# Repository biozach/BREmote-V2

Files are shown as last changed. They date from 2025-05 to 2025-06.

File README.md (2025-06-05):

# BREmote V2 - Open Source eFoil and Esk8 remote 
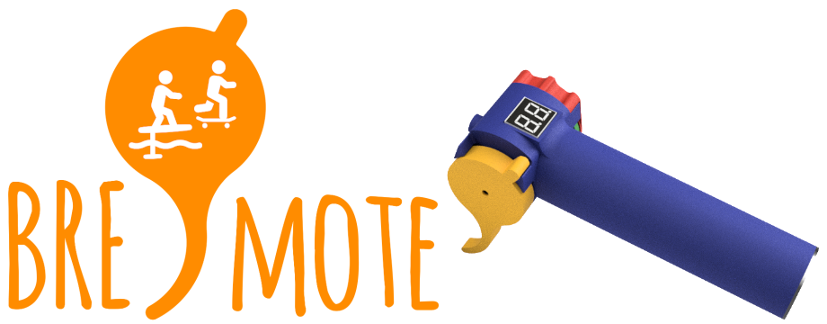
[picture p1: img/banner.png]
Banner


## Features:
* All mechanical parts 3D printed (even the springs)
* Symmetric design
* Sustainable - All external parts can be replaced
* Open Source: 3D Models, Electronics and Software are GPL3.0
* 868/915MHz Link (range dependant on antenna type, position)
* Communication with VESC via UART / CAN
* Low battery alarm (vibration)
* Water ingress alarm integrated in receiver
* Gears / Power Levels / Cruise Control
* Charging and Programming via USB

## Links:
* [Build Video](https://youtu.be/Fw4YdQWvs6I)
* [SW Setup & Config Video](https://youtu.be/r6JIZEq3aTU)
* [Config Tool](https://lbre.de/BREmote/struct.html)
* [Serial Terminal](https://lbre.de/BREmote/sertest.html)
* [Expo Tool](https://lbre.de/BREmote/expo.html)
* [Flash Download Tool](https://dl.espressif.com/public/flash_download_tool.zip)

## Usage:

## Status/Error Codes:
Tx:
* Ex : Remote Errors
* EP: Not paired
* EC: Not Cald
* ESV: Error Config version SPIFFS <> Build
* ESP3: Error init SPIFFS
* ESP4: Error writing SPIFFS
* EHFC: Error HF (LoRa) setting
* EHFI: Error HF (LoRa) init
* EHFP: Error transmit power
* ECH: Error charger

Rx:
* Aux blink:
	* 3x: Error init SPIFFS
	* 2x: Error Config version SPIFFS <> Build
	* 4x: Error writing SPIFFS

* Bind blink:
	* Short Periodic Flash: Not paired
	* Blink: Paired not connected
	* Solid: Connected
	
	* 2: Error transmit power
	* 3: Error HF (LoRa) setting
	* 4: Error HF (LoRa) init

## Inputs at startup:
Tx:
* Left: Calibrate
* Right: Pair
* THR+Left: USB Mode
* THR+Right: Delete Spiffs

Rx:
* Bind pushed: Pair
* Both pushed: Delete config

# Connection Examples:

<details>
<summary>VESC with UART</summary>

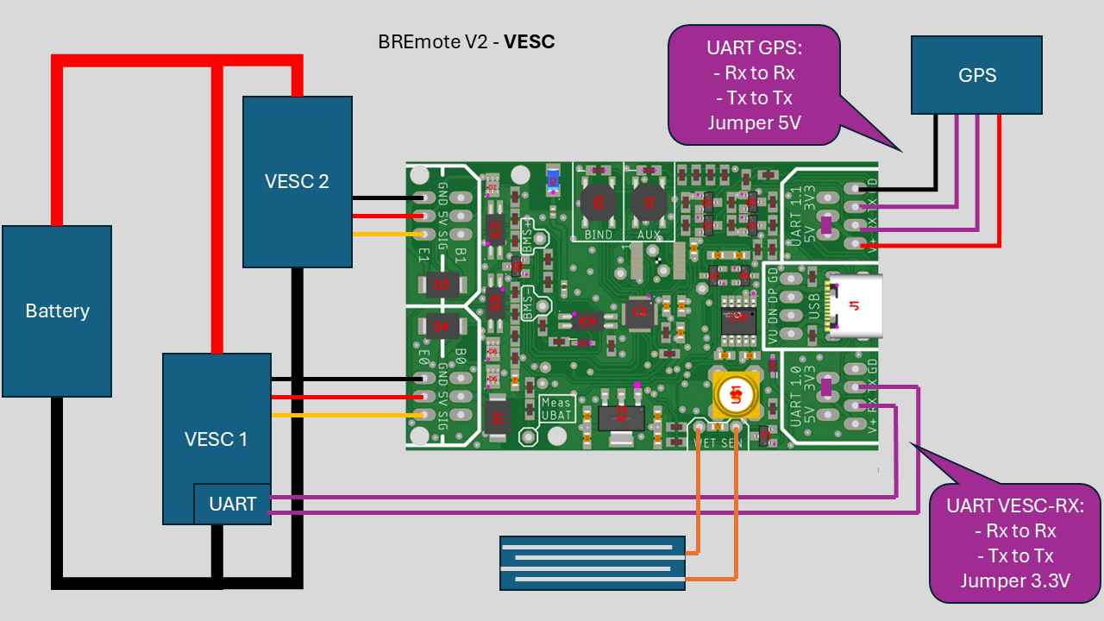
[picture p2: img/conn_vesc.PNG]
Conn


</details>

<details>
<summary>ESC with BREmote BEC</summary>

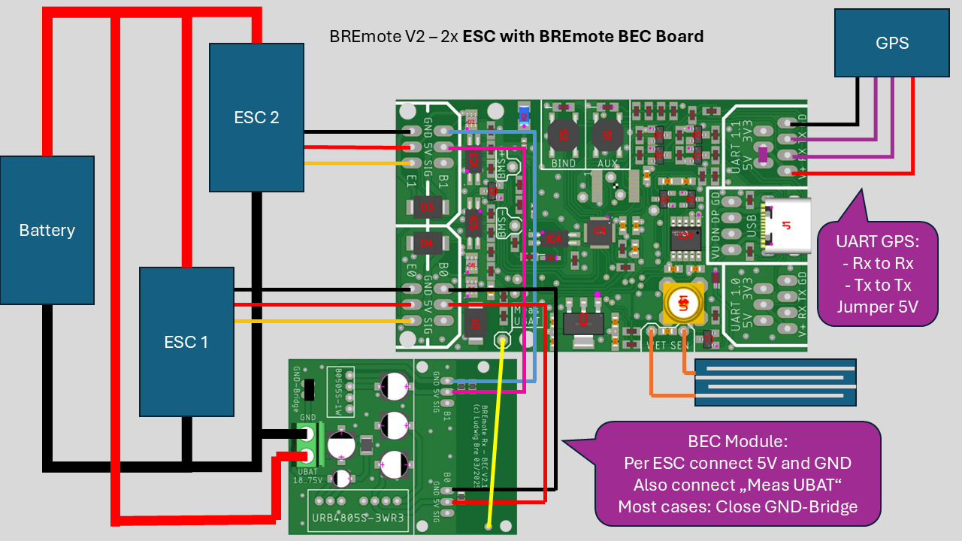
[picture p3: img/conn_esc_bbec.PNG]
Conn


</details>

<details>
<summary>ESC with own BEC</summary>

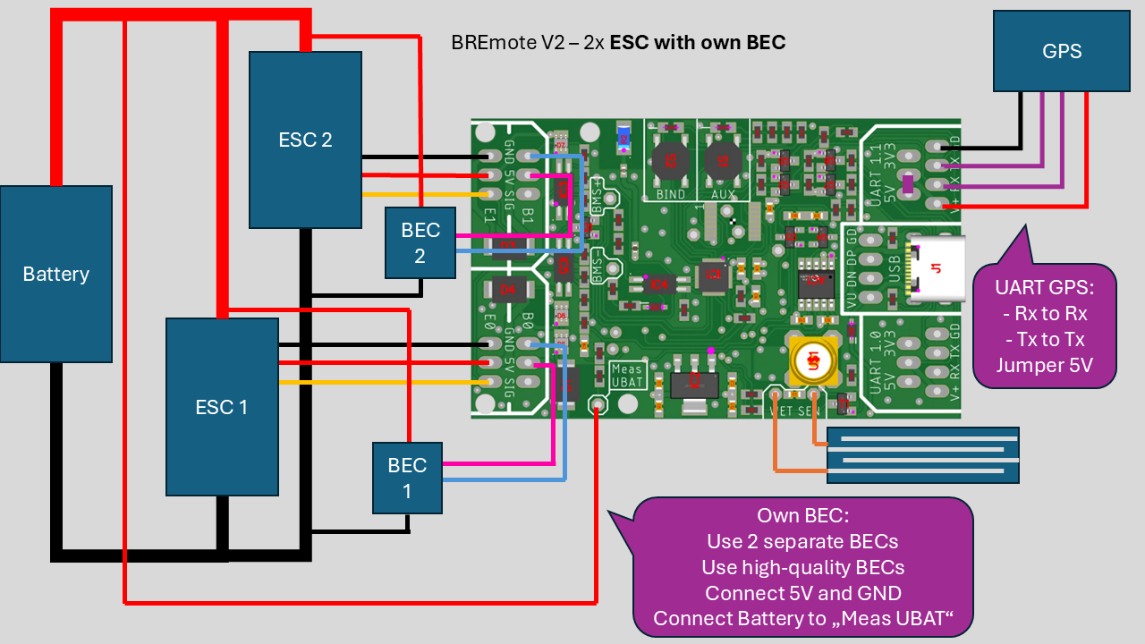
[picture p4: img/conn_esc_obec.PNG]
Conn


</details>

<details>
<summary>VESC + Servo</summary>

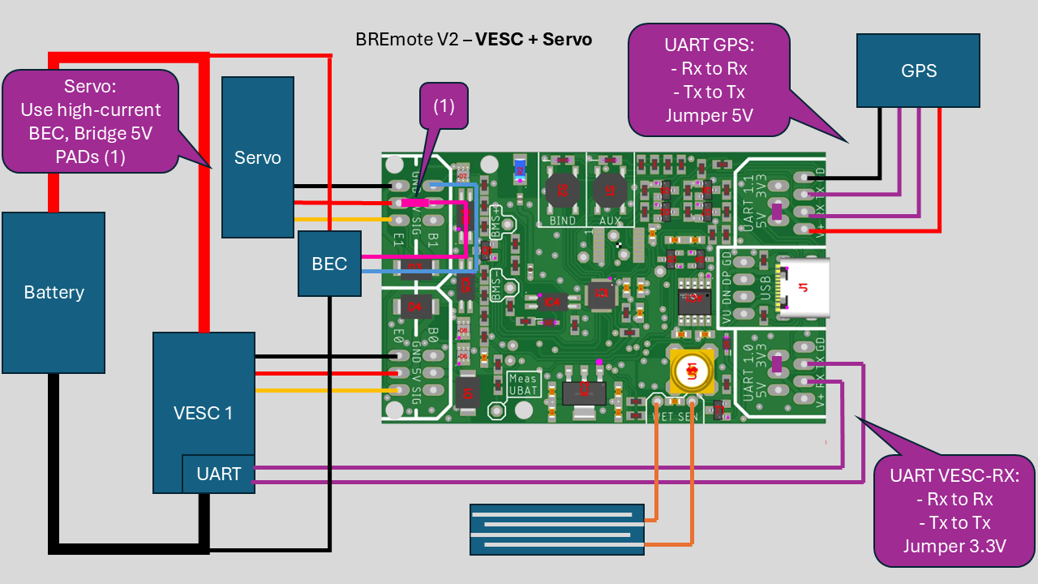
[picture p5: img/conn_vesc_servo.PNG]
Conn


</details>

<details>
<summary>ESC + Servo</summary>

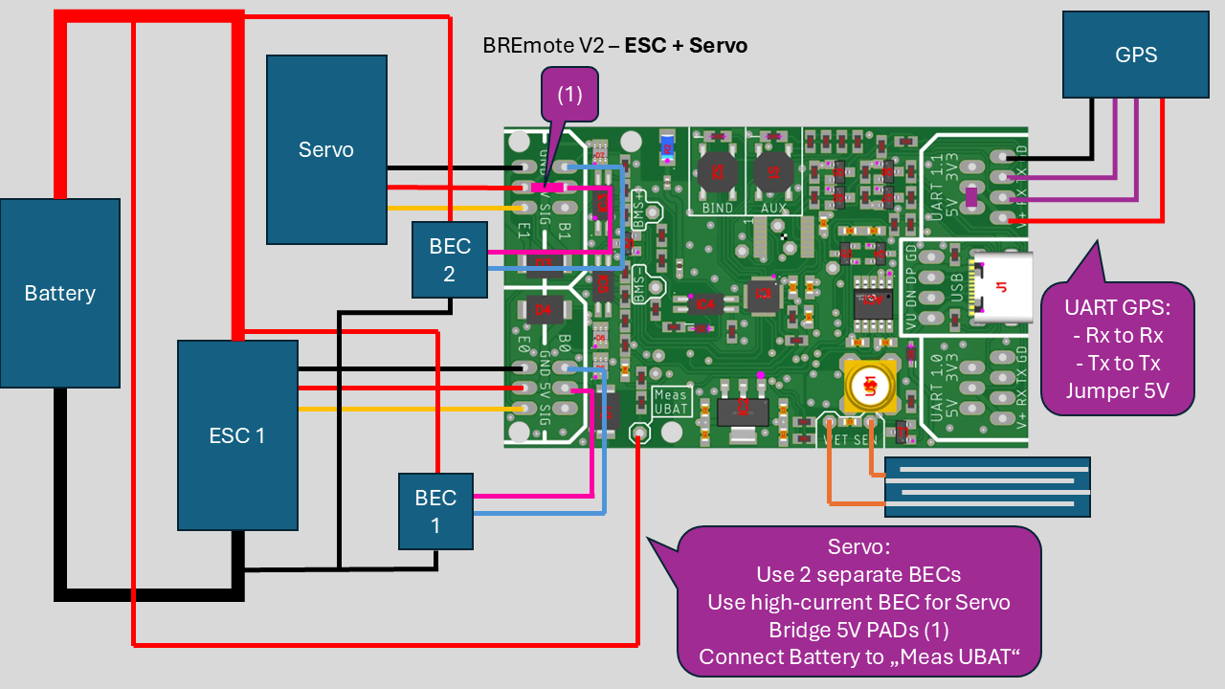
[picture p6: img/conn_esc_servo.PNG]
Conn


</details>

# Changelog:
### 2025-06-05:
Updated Readme (Add YT link and conn examples)
### 2025-05-26:
Updated Complete.step (spring assy. missing)
Added RF settings for US/AU(915MHz) in Tx&Rx
### 2025-05-20: [Release V2.1]
Initial release

---
# Credits:
Logo uses "watersport" and "Skate" by Adrien Coquet from https://thenounproject.com/. CC BY 3.0.

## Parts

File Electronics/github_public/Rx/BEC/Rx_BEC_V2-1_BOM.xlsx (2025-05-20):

Comment | Designator | Footprint | JLCPCB Part #（optional）
100uF 35V RVE100UF35V67RV0072 | C3 | CPOL-EU153CLV-0605 | C2836437
10uF 100V RVT2A100M0607 | C2, C4, C5 | CPOL-EU153CLV-0605 | C86606 | C72482
10uH 900mA CBC3225T100KR | L1 | R-EU_R1210 | C90321
1uF 100V HT2A1R0M0405 | C1 | CPOL-EU153CLV-0405 | C87863
470 | R1, R2, R3 | R-EU_R0805
WJ126V-5.0-2P | U$1 | WJ126V-5.0-2P | C8404

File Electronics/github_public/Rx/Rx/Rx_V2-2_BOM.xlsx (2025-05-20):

Comment | Designator | Footprint | JLCPCB Part #（optional）
0R | R_ANT | R-EU_R0402
100 | R7, R8 | R-EU_R0603
100n | C1, C2, C3, C4, C7, C8, C9, C10, C13, C16 | C-EUC0603
10k | R4, R10, R11, R15, R20, R24, R28, R30, R31, R32, R33, R34, R35, R36, R37 | R-EU_R0603
120k | R1 | R-EU_R0603
1M | R22 | R-EU_R0603
1N4148WS | D2, D5 | 1N4148WS | C2128
1k | R9, R14, R38, R39, R40, R41, R42 | R-EU_R0603
1u | C5, C6, C12 | C-EUC0603
2.2uF | C11 | C-EUC0603
220 | R25, R26 | R-EU_R0603
3k3 | R12 | R-EU_R0603
4k7 | R13, R16, R17, R18 | R-EU_R0603
5k1 | R5, R6 | R-EU_R0603
LQW15AN6N8G00D | L_ANT1 | R-EU_R0402 | C82919
74HC4052PW,118 | IC6 | 74HC4052PW,118 | C19723807
AMS1117-3.3 | IC2 | AMS1117-3.3 | C6186
AO3400A | Q3, Q4 | AO3400A | C20917
AW9523BTQR | IC1 | AW9523BTQR | C148077
BSS138 | Q1, Q2, Q5, Q6, Q7 | BSS138 | C5224260
CH340K | AC1 | CH340K | C968586 | alt C18208922
EL3H7_TA_-VG | IC3, IC4, IC5 | EL3H7_TA_-VG | C32565
LM66100DCKR | D6, D7, D8 | LM66100DCKR | C2869734
MMBT5551 | T1 | BC847B-NPN-SOT23-BEC | C2145
KT-0603R | LED2, LED3 | LEDCHIP-LED0805 | C2286
P6SMB6.8CA | D1, D3, D4 | P6SMB6.8CA | C78395
RFANT3216120A5T | R2 | R-EU_R1206 | C127629
BWSMA-KE-Z001 | U$1 | SMA_5.08_1.4 | C496549
TS-1187A-B-A-B | S1, S2 | TS-1187A-B-A-B | C318884
TYPE-C-31-M-12 | J1 | TYPE-C-31-M-12 | C165948

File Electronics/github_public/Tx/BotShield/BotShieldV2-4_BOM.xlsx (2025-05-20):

Comment | Designator | Footprint | JLCPCB Part #（optional）
100 | R4 | R-EU_R0603
100n | C5, C6, C9, C10, C13, C14, C15, C17, C20 | C-EUC0603
10k | R10, R11, R13, R14, R15, R16, R17, R22 | R-EU_R0603
10n | C12 | C-EUC0603
10u | C7, C8, C16 | C-EUC0603
1k | R3, R7, R12, R20, R21 | R-EU_R0603
1u | C18, C19 | C-EUC0603
2.2uF | C11 | C-EUC0603
3k3 | R6, R18 | R-EU_R0603
4k7 | R5, R8, R9 | R-EU_R0603
6k8 | R19 | R-EU_R0603
74LVC1G14GW,125 | IC3 | 74LVC1G14GW,125 | C265125
ADS1115IDGSR | IC5 | ADS1115IDGSR | C37593
AO3400A | Q2, Q3, Q4, Q5 | AO3400A | C20917
AO3401A | Q6 | AO3401A | C15127
CH340K | AC1 | CH340K | C18208922 | alt C968586
DW01A | IC4 | DW01A-G | C2927799 | alt C18164398 or C351410
FPC-05F-14PH15 | U$11 | FPC-05F-14PH15 | C2856818
FS8205A | Q1 | FS8205A | C2830320
ME6211C33M5G-N | IC6 | ME6211C50M5G | C82942
OH49E-S | IC8 | DRV5055A3QDBZR | C85573
SDFL2012Q2R7KTF | L2 | SDFL2012Q2R7KTF | C1046
TP4056 | IC7 | TP4056-42-ESOP8 | C725790

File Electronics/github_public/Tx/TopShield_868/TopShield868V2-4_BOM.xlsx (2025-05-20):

Comment | Designator | Footprint | JLCPCB Part #（optional）
0R | R1 | R-EU_R0603
100n | C1, C3, C4 | C-EUC0603
10k | R23 | R-EU_R0603
np | R24 | R-EU_R0603
LQW15AN4N3B00D | L_ANT | R-EU_R0402 | C91625
GJM1555C1H4R0BB01D | C_ANT | C-EUC0402 | C161323
1u | C2 | C-EUC0603
LQW15AN6N8G00D | L_ANT1 | R-EU_R0402 | C82919
FPC-05F-14PH15 | U$6 | FPC-05F-14PH15 | C2856818
HT16K33A-24SSOP | U$1 | HT16K33A | C5444736 | alt C5444738
OH49E-S | IC1 | DRV5055A3QDBZR | C85573
RFANT3216120A5T | R2 | R-EU_R1206 | C127629
SDFL2012Q2R7KTF | L1 | SDFL2012Q2R7KTF | C1046
UHE4913G-AE3-R | IC2 | DRV5055A3QDBZR | C86815

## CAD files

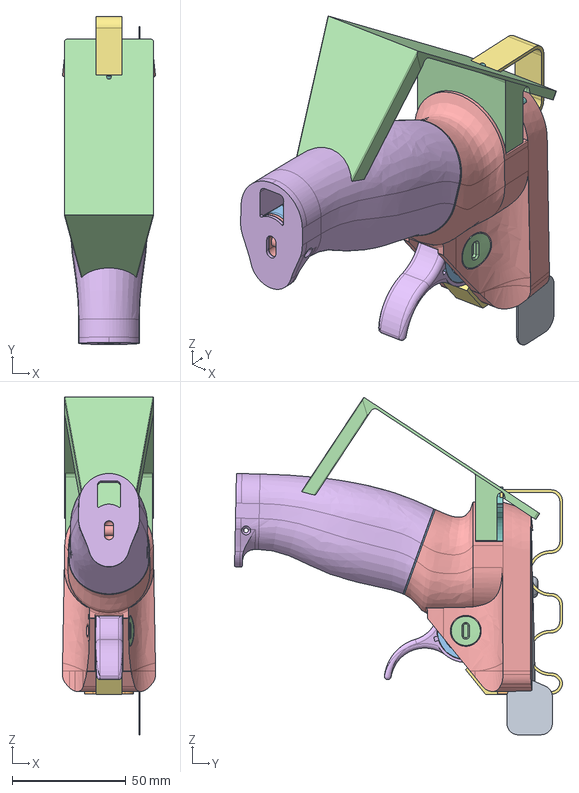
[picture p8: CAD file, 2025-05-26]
Mechanics/Complete.step
41.0 x 144.3 x 148.6 mm
Switch_Side
V2_Spring_Metal v1

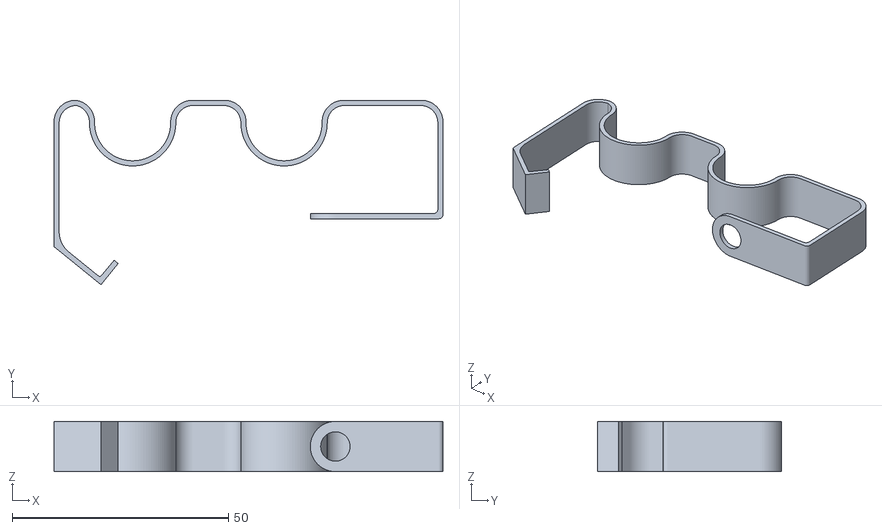
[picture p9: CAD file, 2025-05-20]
Mechanics/Assy_Clamp.stl
90.0 x 42.7 x 11.6

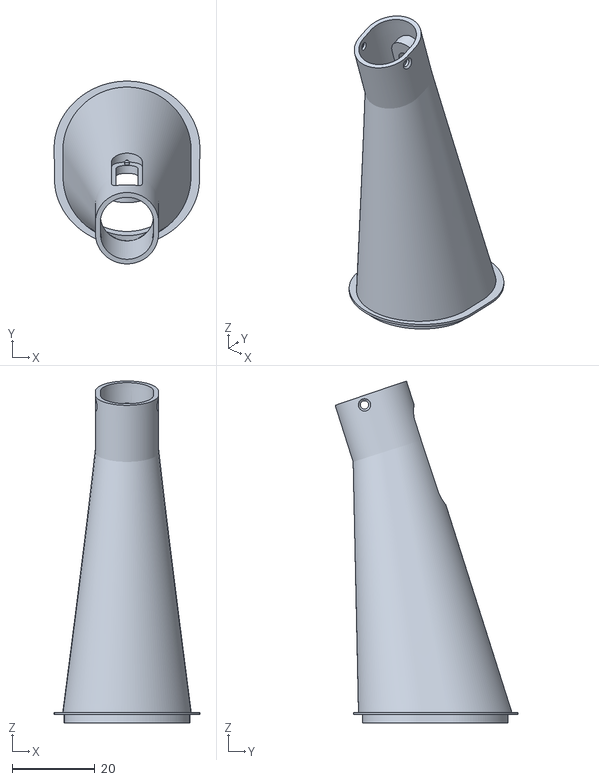
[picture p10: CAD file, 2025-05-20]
Mechanics/InsideHandle.stl
35.3 x 44.3 x 82.9

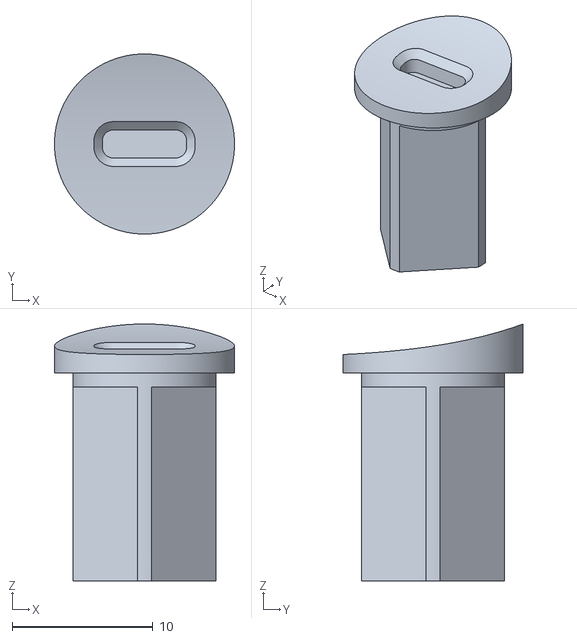
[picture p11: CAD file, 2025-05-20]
Mechanics/Trigger_Pin.stl
12.8 x 12.8 x 18.3

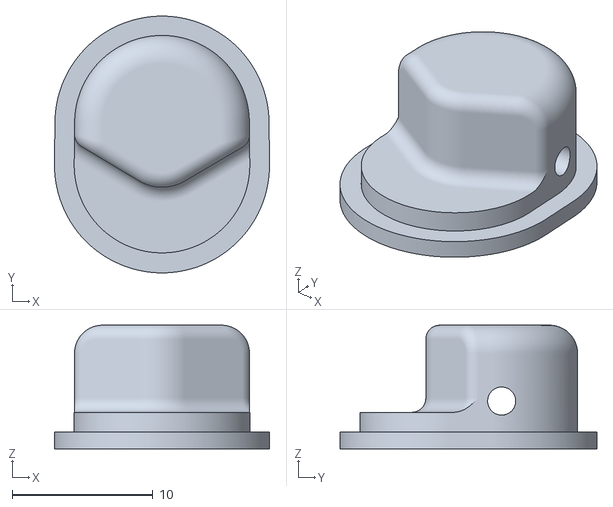
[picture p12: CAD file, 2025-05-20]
Mechanics/Endcap_Handle.stl
15.3 x 18.3 x 8.80

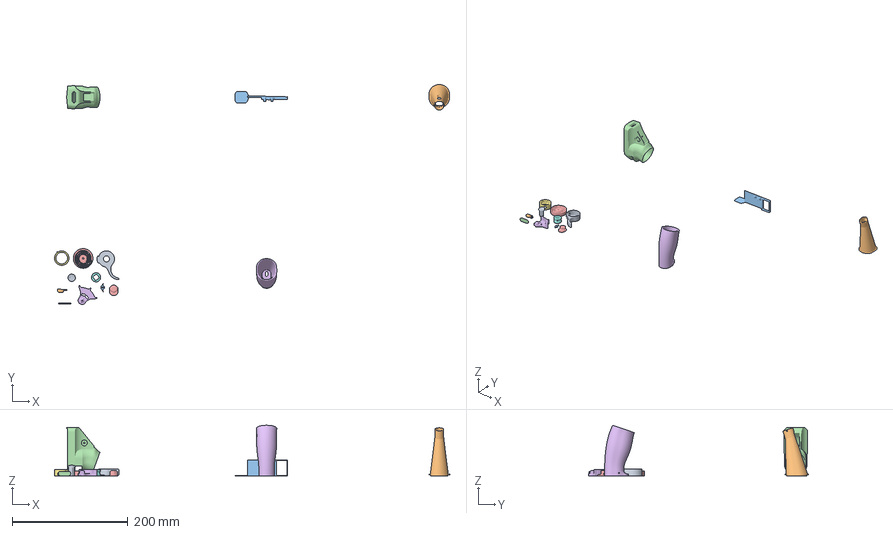
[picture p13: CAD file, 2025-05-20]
Mechanics/AllPartsSliced_V2-1.3mf
681.3 x 379.3 x 87.2 mm
XX_Trigger_export_steep.stl
XX_InsideHandle.stl
XX_Top_Cover.stl
Top.stl
Stator_export.stl
Rotor.stl
XX_Spring_Idle_Mod_Rot (1) (1).stl
XX_Spring_Idle_Mod_Rot (1).stl
XX_Trigger_Pin_Export.stl
Switch.stl
Switch_Cover.stl
FrontPlate.stl
Endcap_Handle.stl
HandleSmall.stl

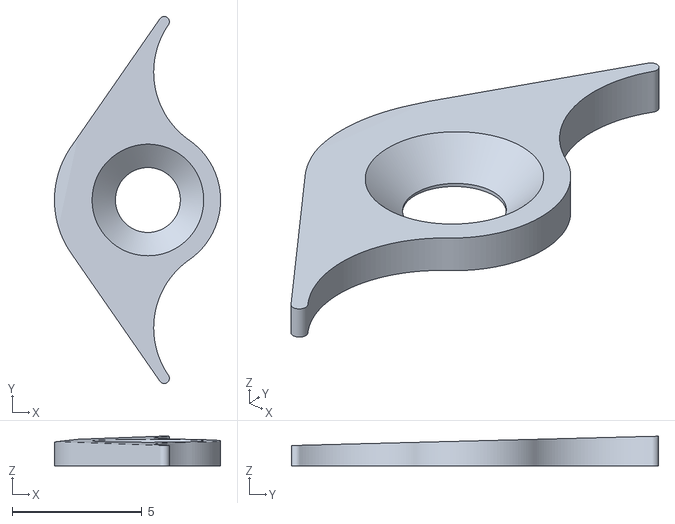
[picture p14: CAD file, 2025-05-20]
Mechanics/Switch_Cover.stl
6.40 x 14.1 x 1.14

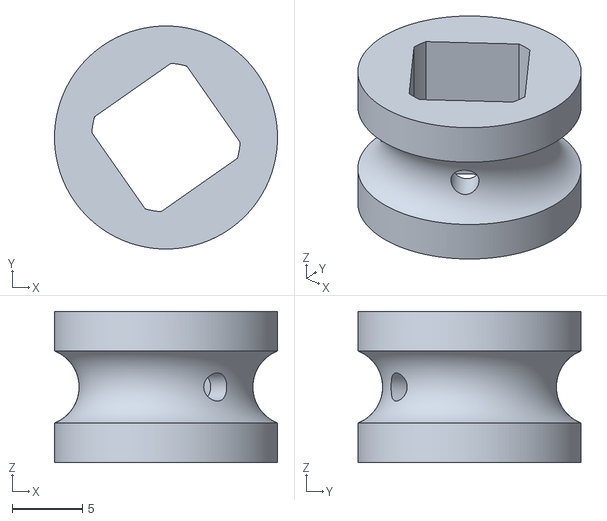
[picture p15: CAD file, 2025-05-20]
Mechanics/Trigger_Spring_2.stl
15.9 x 15.9 x 10.8

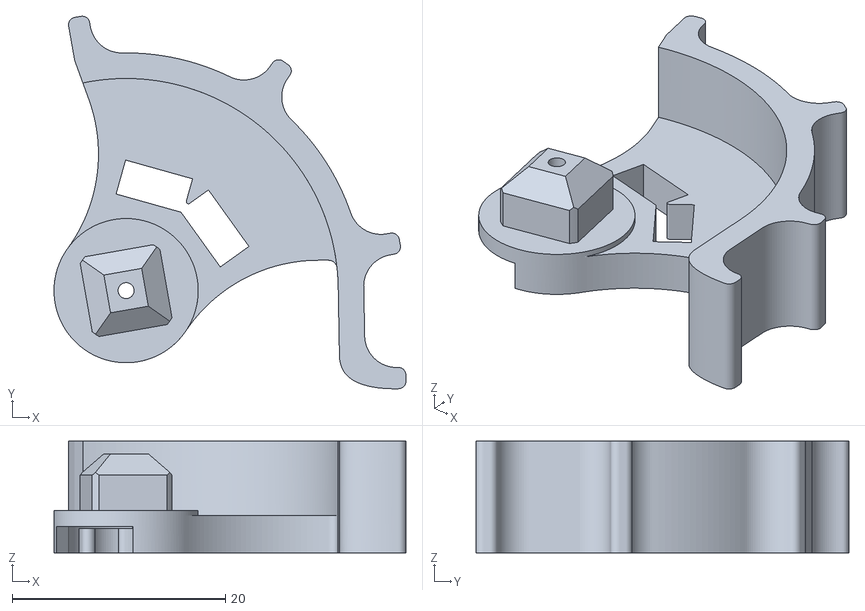
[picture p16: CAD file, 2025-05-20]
Mechanics/Rotor_sidegrip.stl
33.0 x 35.0 x 10.5

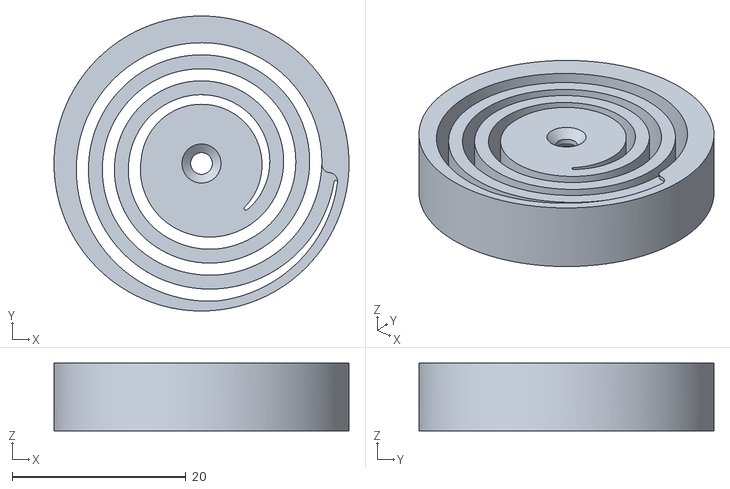
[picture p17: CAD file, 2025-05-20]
Mechanics/Stator.stl
34.0 x 34.0 x 7.80

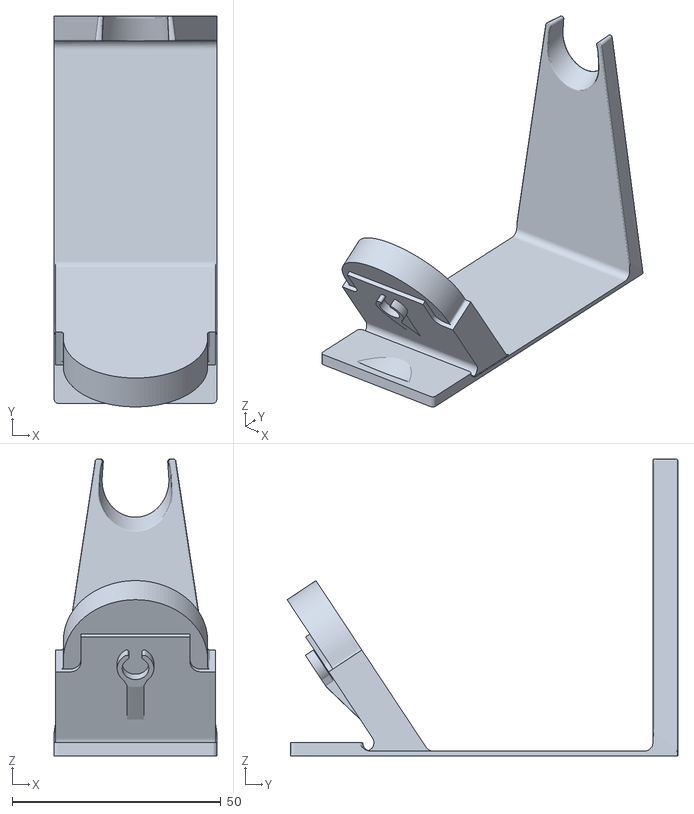
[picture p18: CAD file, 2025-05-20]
Mechanics/FillStand.stl
39.0 x 93.7 x 71.2

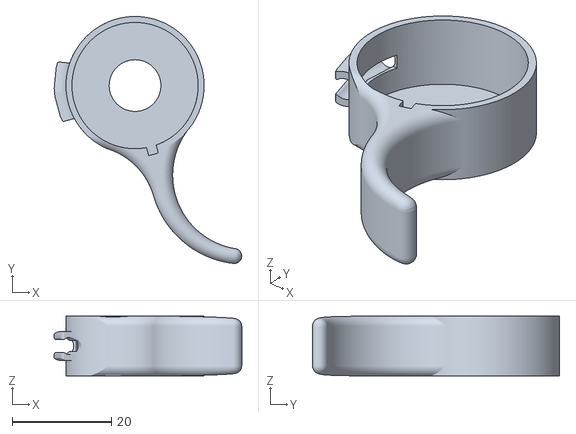
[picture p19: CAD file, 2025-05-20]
Mechanics/Trigger.stl
37.7 x 49.7 x 12.0

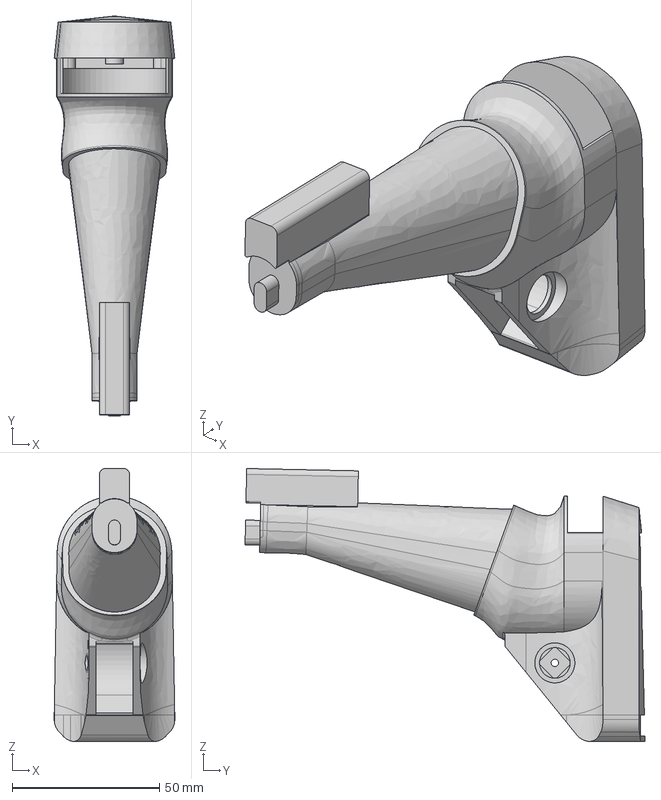
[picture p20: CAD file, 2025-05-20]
Mechanics/HandleCutter.step
41.0 x 135.9 x 92.8 mm

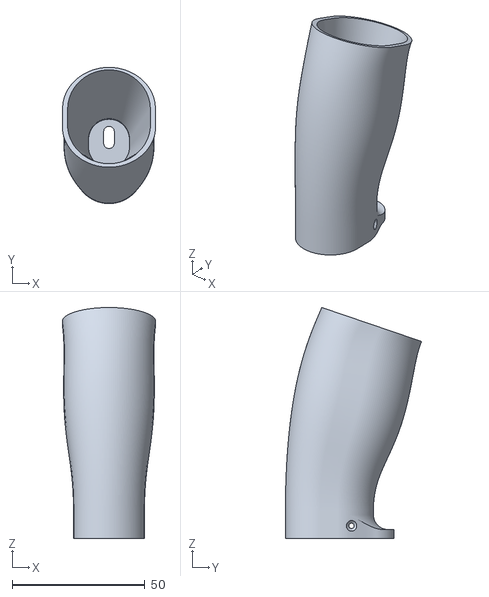
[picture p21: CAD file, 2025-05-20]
Mechanics/HandleSmall.stl
35.2 x 51.4 x 87.2

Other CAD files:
Mechanics/Trigger_Spring_1.stl
Mechanics/Top.stl
Mechanics/Switch.stl
Mechanics/Rotor.stl
Mechanics/FrontPlate.stl
Mechanics/Top_Cover.stl

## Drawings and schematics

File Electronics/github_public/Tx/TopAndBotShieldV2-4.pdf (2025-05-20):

05.05.2025 14:25 f=0.80 C:\Users\rcb8fe\Desktop\prep_order\Tx\final\github_public\TopAndBotShieldV2-4.sch (Sheet: 1/1) ¹⁰uF shared with TP⁴⁰⁵⁶ | 24⁻pin: Place 0R
R7 6 | C¹

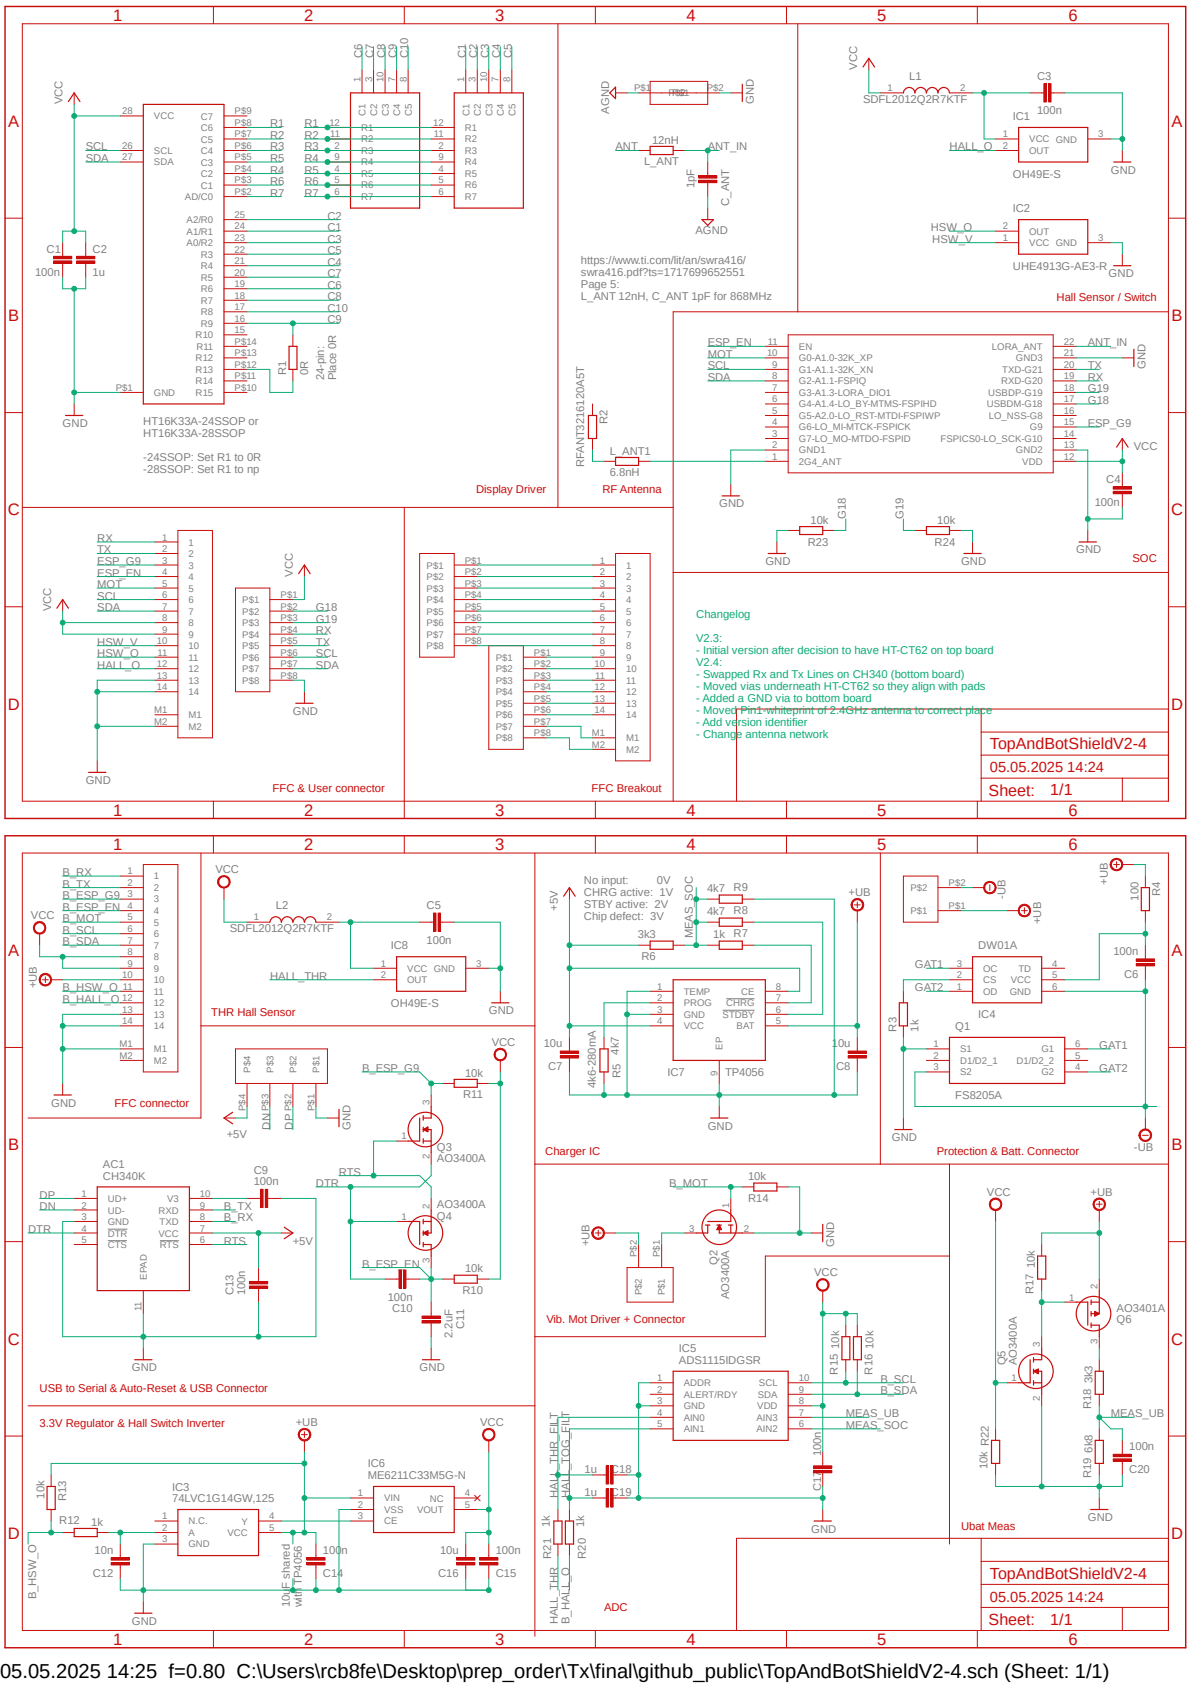
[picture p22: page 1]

SDFL2012Q2R7KTF VCC GND AGND VCC

https://www.ti.com/lit/an/swra416/
swra416.pdf?ts=1717699652551
Page 5:
L_ANT 12nH, C_ANT 1pF for 868MHz

Changelog
- Initial version after decision to have HT-CT62 on top board
- Swapped Rx and Tx Lines on CH340 (bottom board)
- Moved vias underneath HT-CT62 so they align with pads
- Added a GND via to bottom board
- Moved Pin1-whiteprint of 2.4GHz antenna to correct place
- Add version identifier
- Change antenna network

VCC | No input: 0V

Vib. Mot Driver + Connector

USB to Serial & Auto-Reset & USB Connector

VCC 10k
3.3V Regulator & Hall Switch Inverter

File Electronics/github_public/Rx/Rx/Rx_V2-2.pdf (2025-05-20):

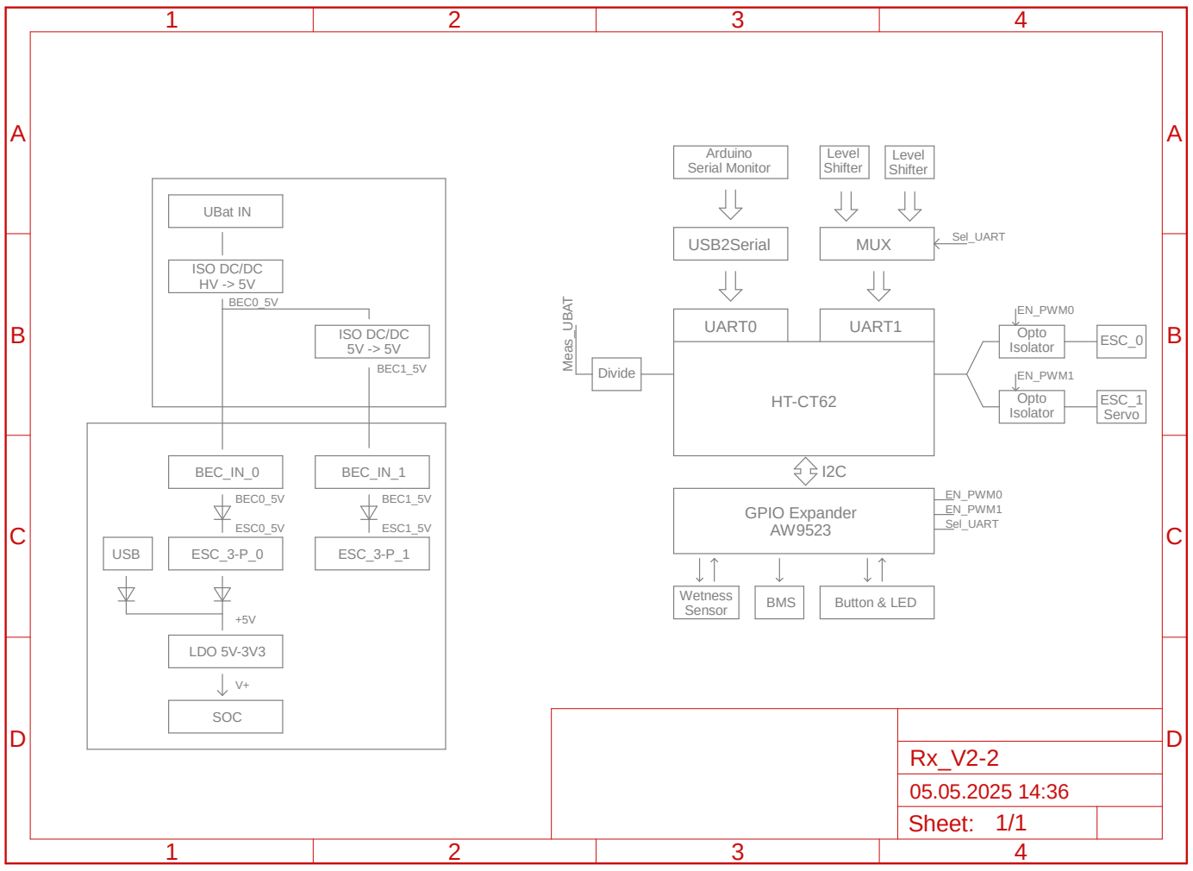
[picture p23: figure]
UART0; UART1; USB2Serial; MUX; Level Shifter; Arduino Serial Monitor; Opto Isolator; ESC_0; ESC_1 Servo; EN_PWM0; EN_PWM1; Sel_UART; Divide Meas_UBAT; GPIO Expander AW9523; I2C Wetness Sensor; BMS; Button & LED; EN_PWM0 EN_PWM1 Sel_UART; BEC_IN_0; ESC_3-P_0; LDO 5V-3V3; BEC_IN_1; ESC_3-P_1; SOC; ISO DC/DC HV -> 5V; ISO DC/DC; 5V -> 5V UBat IN; USB; ESC0_5V; BEC0_5V; BEC1_5V; ESC1_5V; Sheet:

05.05.2025 14:57 f=1.05 C:\Users\rcb8fe\Desktop\prep_order\Tx\final\openfoil\Rx\Rx_V2-2.sch (Sheet: 1/1)

# 1k GND

# IC3 A

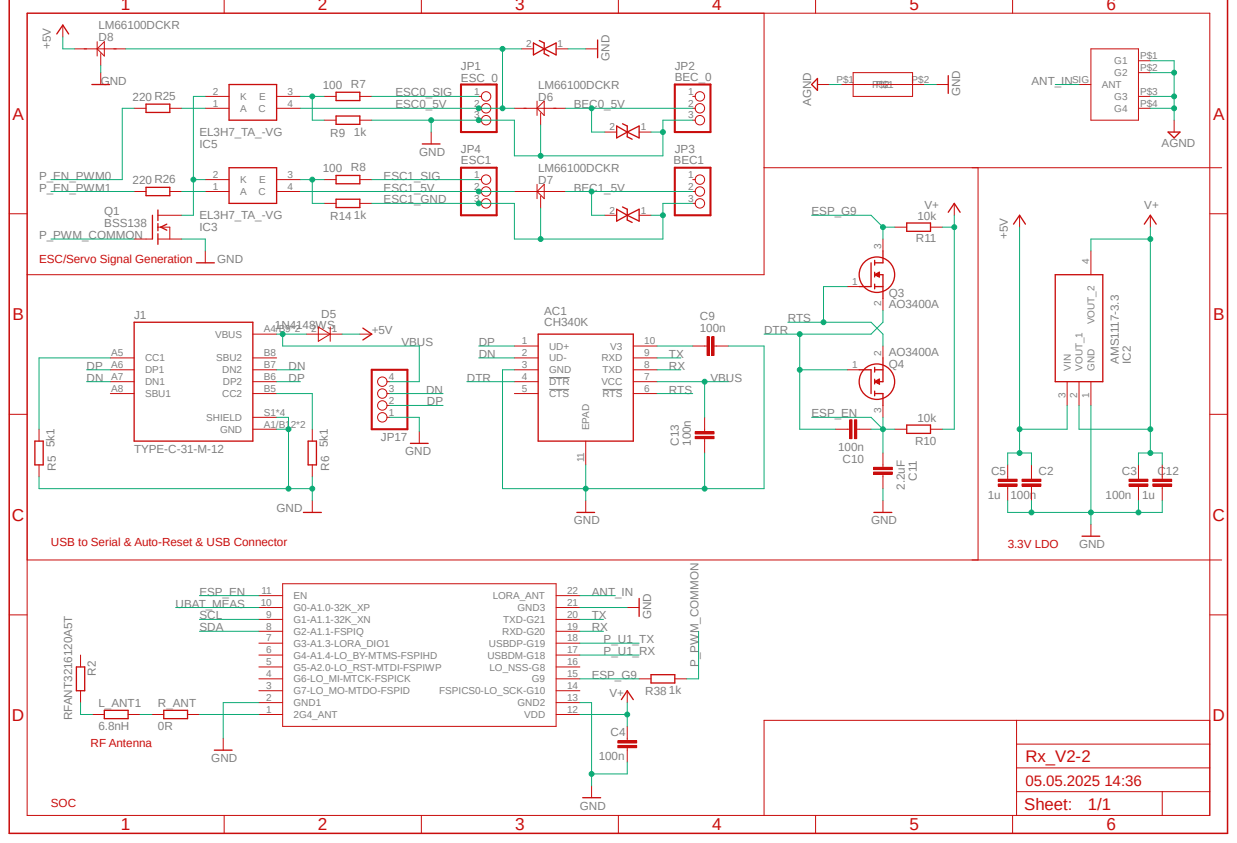
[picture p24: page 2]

ESC/Servo Signal Generation

V+ | BSS¹³⁸ 10k | 10k

A

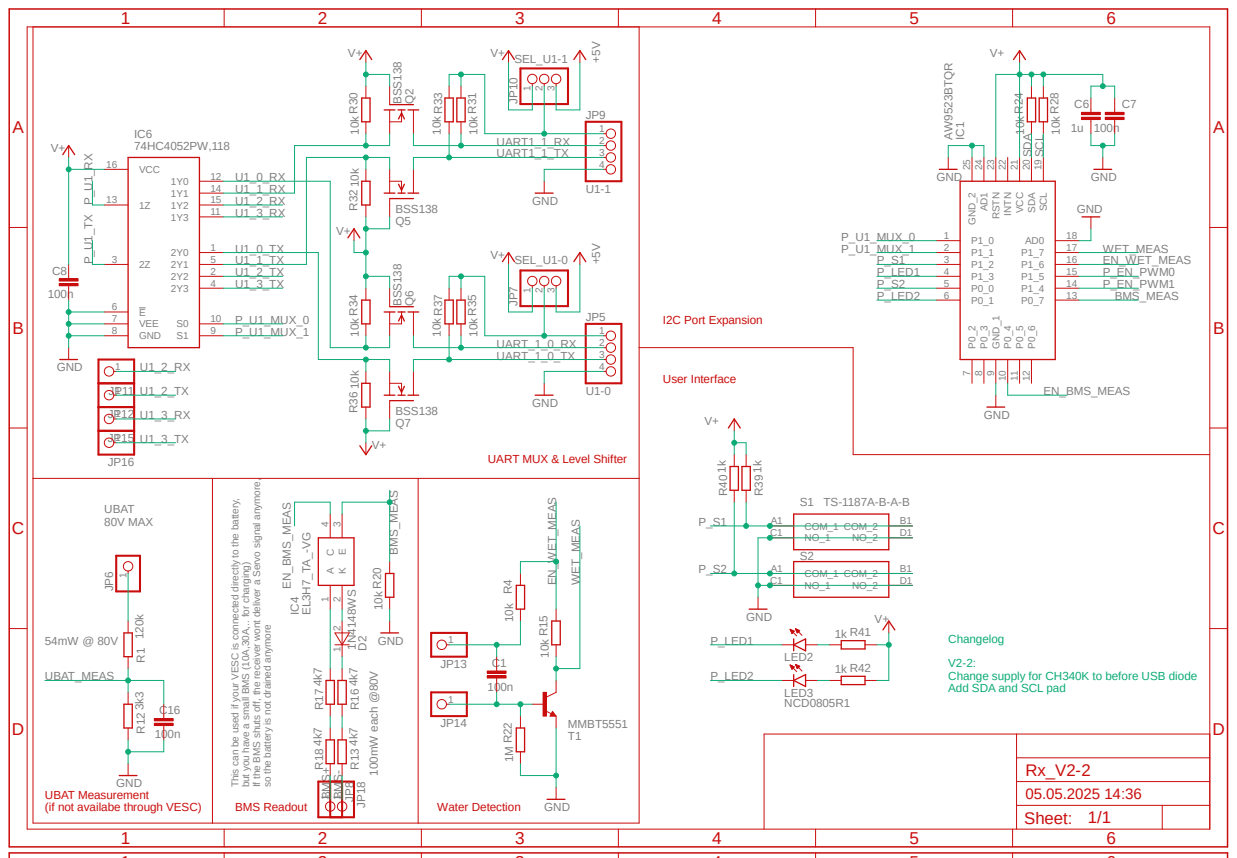
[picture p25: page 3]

UART MUX & Level Shifter

Changelog
Change supply for CH340K to before USB diode
Add SDA and SCL pad

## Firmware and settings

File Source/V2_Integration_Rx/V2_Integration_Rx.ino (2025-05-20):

#include "BREmote_V2_Rx.h"

SX1262 radio = new Module(P_LORA_NSS, P_LORA_DIO, P_LORA_RST, P_LORA_BUSY);
Adafruit_AW9523 aw;
Ticker ticksrc;
TinyGPSPlus gps;

void setup()
{
  enterSetup();

  Wire.begin(P_I2C_SDA, P_I2C_SCL); //SDA, SCL
  Wire.setClock(400000); // Set to 400 kHz
  startupAW();

  initSPIFFS();
  getConfFromSPIFFS();

  startupRadio();
  radio.setPacketReceivedAction(packetReceived);
  radio.implicitHeader(6);
  radio.startReceive();

  checkButtons();

  rxIsrState = 1;

  initRMT();

  Serial1.begin(115200, SERIAL_8N1, P_U1_RX, P_U1_TX);
  
  aw.digitalWrite(AP_EN_PWM0, 1);
  aw.digitalWrite(AP_EN_PWM1, 1);

  triggerReceiveSemaphore = xSemaphoreCreateBinary();
  loopTaskHandle = xTaskGetCurrentTaskHandle();
  
  //Runs every 10ms to generate both PWM signals, high prio
  xTaskCreatePinnedToCore(generatePWM, "Generate_PWM_10ms", 2048, NULL, 10, &generatePWMHandle, 0);
  //Runs upon RF interrupt and reads packet & responds, medium-high prio
  xTaskCreatePinnedToCore(triggeredReceive, "RF_ReceiveTask_triggered", 2048, NULL, 5, &triggeredReceiveHandle, 0);

  //Checks if there is connection and blinks LED, low prio
  xTaskCreatePinnedToCore(checkConnStatus, "Check_conn_staus_200ms", 2048, NULL, 2, &checkConnStatusHandle, 0);

  configureGPS();

  exitSetup();
  PWM_active = 1;
  
  //pinMode(P_UBAT_MEAS, OUTPUT);
}

unsigned long loop_timer = 0;

void loop()
{
  checkSerial();

  if(millis()-loop_timer > 1000)
  {
    loop_timer = millis();
    if(usrConf.wet_det_active)
    {
      checkWetness();
    }

    if(usrConf.gps_en)
    {
      getGPSLoop();
    }

    if(usrConf.data_src == 1)
    {
      getUbatLoop();
    }
    else if(usrConf.data_src == 2)
    {
      getVescLoop();
    }
  }

  //telemetry.foil_speed = (millis()/1000) % 100;

  vTaskDelay(pdMS_TO_TICKS(10));
}

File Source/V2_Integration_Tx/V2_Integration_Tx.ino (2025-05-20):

#include "BREmote_V2_Tx.h"

SX1262 radio = new Module(P_LORA_NSS, P_LORA_DIO, P_LORA_RST, P_LORA_BUSY);
Adafruit_ADS1115 ads;
Ticker ticksrc;

void setup()
{
  enterSetup();

  Wire.begin(P_I2C_SDA, P_I2C_SCL); //SDA, SCL
  Wire.setClock(400000); // Set to 400 kHz
  startupDisplay();

  initSPIFFS();
  getConfFromSPIFFS();

  startupADS();

  checkCharger();

  startupRadio();
  radio.setDio1Action(packetReceived);

  //Runs every 100ms and sends data to Rx, medium prio
  xTaskCreatePinnedToCore(sendData, "Send_Data_100ms", 2048, NULL, 5, &sendDataHandle, 0);
  //Triggered by senData, waits from telem from Rx after sending data to it
  xTaskCreatePinnedToCore(waitForTelemetry, "wait_for_telem_triggered", 2048, NULL, 4, &triggeredWaitForTelemetryHandle, 0);
  //Measure, Buffer and calculate inputs
  xTaskCreatePinnedToCore(measBufCalc, "wait_for_telem_triggered_10ms", 2048, NULL, 6, &measBufCalcHandle, 0);
  //Update bargraphs
  xTaskCreatePinnedToCore(updateBargraphs, "wait_for_telem_triggered_200ms", 2048, NULL, 6, &updateBargraphsHandle, 0);

  //Show boot animation and display internal battery voltage (needed for buffers)
  bootAnimation();
  //Check if calibration is valid, otherwise calibrate
  checkCal();
  //Check if a button combination is input
  checkStartupButtons();
  //Check if system is paired
  checkPairing();

  if(usrConf.no_lock)
  {
    while(thr_scaled > 10)
    {
      advanceArrow();
      delay(100);
    }
    system_locked = 0;
  }
  if(usrConf.no_gear)
  {
    gear = usrConf.max_gears;
  }
  else
  {
    if(usrConf.startgear > usrConf.max_gears) usrConf.startgear = usrConf.max_gears;
    gear = usrConf.startgear+1;
  }  

  exitSetup();
}

void loop()
{
  runMenu();
  if(in_menu > 0) in_menu--;

  checkSerial();

  if(remote_error == 0)
  {
    if(system_locked)
    {
      displayLock();
    }
    else
    {
      if(telemetry.foil_speed != 0xFF)
      {
        displayDigits(telemetry.foil_speed/10,telemetry.foil_speed-10*(telemetry.foil_speed/10));
      }
      else
      {
        displayDigits(DASH, DASH);
      }
      updateDisplay();
    }
  }
  else
  {
    displayDigits(LET_E, remote_error);
  }
  
  delay(110);
  
} //End of loop()

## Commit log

2025-05-26 Update Complete.step & add RF US/AU915
    [Complete.step]
2025-06-05 Added Bridge Info For Servo Option
2025-06-30 fix PWM bug
